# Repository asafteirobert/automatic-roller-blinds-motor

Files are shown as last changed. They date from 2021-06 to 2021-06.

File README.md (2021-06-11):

# Automatic roller blinds motor
Automatic window roller blinds that can be controlled wirelessly using a NRF24L01 module. Controlled either by a small remote, web interface or RESTful API.
Built around an Arduino pro mini and a cheap stepper motor.

For the small remote see this project: [automatic roller blinds small remote](https://github.com/asafteirobert/automatic-roller-blinds-remote).

For the web gateway see this project: [automatic roller blinds web interface](https://github.com/asafteirobert/automatic-roller-blinds-web-ui).

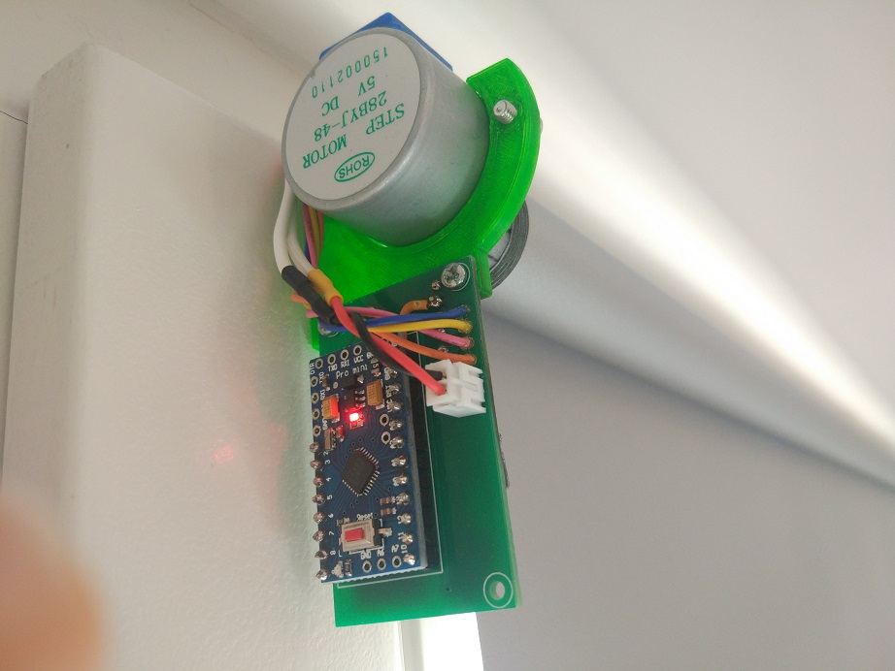
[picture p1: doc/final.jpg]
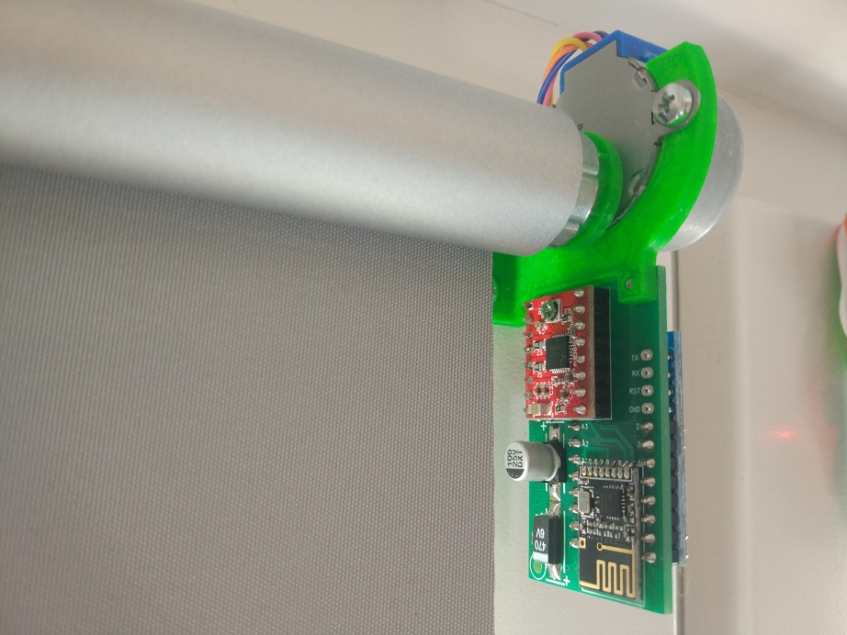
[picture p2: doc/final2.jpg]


https://user-images.githubusercontent.com/6178920/121724726-9242b200-cae8-11eb-8f0c-250091bc018d.mov

## How to use it

This assembly replaces the side of the roller blinds with the string. This means they can no longer be lowered or raised manually.
You will need to route a wire to each window, in order to supply the 9V required.

The blinds are controlled by either the [automatic roller blinds small remote](https://github.com/asafteirobert/automatic-roller-blinds-remote) or the [automatic roller blinds web interface](https://github.com/asafteirobert/automatic-roller-blinds-web-ui), or both.

For more details on how to control and calibrate the blinds, see the related projects linked above. 

## Supported roller blinds

I created this project around a Polish brand(STOL-KAR) of clip-on roller blinds I got from here: https://www.leroymerlin.pl/dekoracja-okien/rolety-i-zaluzje/rolety/roleta-zaciemniajaca-blackout-73-x-150-cm-szara-termoizolacyjna,p575054,l929.html

The shaft has an internal diameter of 18mm.
You will likely need to modify the 3D printed files to adapt for your model. For easier modification, I included the STEP files.

## Limitations and known issues:
- The movement can be slow for some. It takes around 50 seconds to lower and 90 seconds to raise the blinds. Using a bigger stepper motor, such as those used in 3D printers can significantly increase the speed, but would require a much bigger power supply.
- When the blinds are not moving, power is not applied to the stepper motor. This means the blinds can be manually pulled, requiring recalibration.
- There is no encoder, so if the motor gets stuck, misses steps or the blinds are rotated manually, recalibration is needed. Also there are no endstops.

## Making your own
All the required files are included in this project. This includes source code, 3D files to be 3D printed, schematic and PCB.
For instructions see [doc/assembly.md](doc/assembly.md).

## Project status: Finished, active
All intended functionality is implemented and manually tested. I will try to fix major bugs when they are reported. I will review pull requests, but generally I prefer if you fork the project in order to make your own changes and improvements.

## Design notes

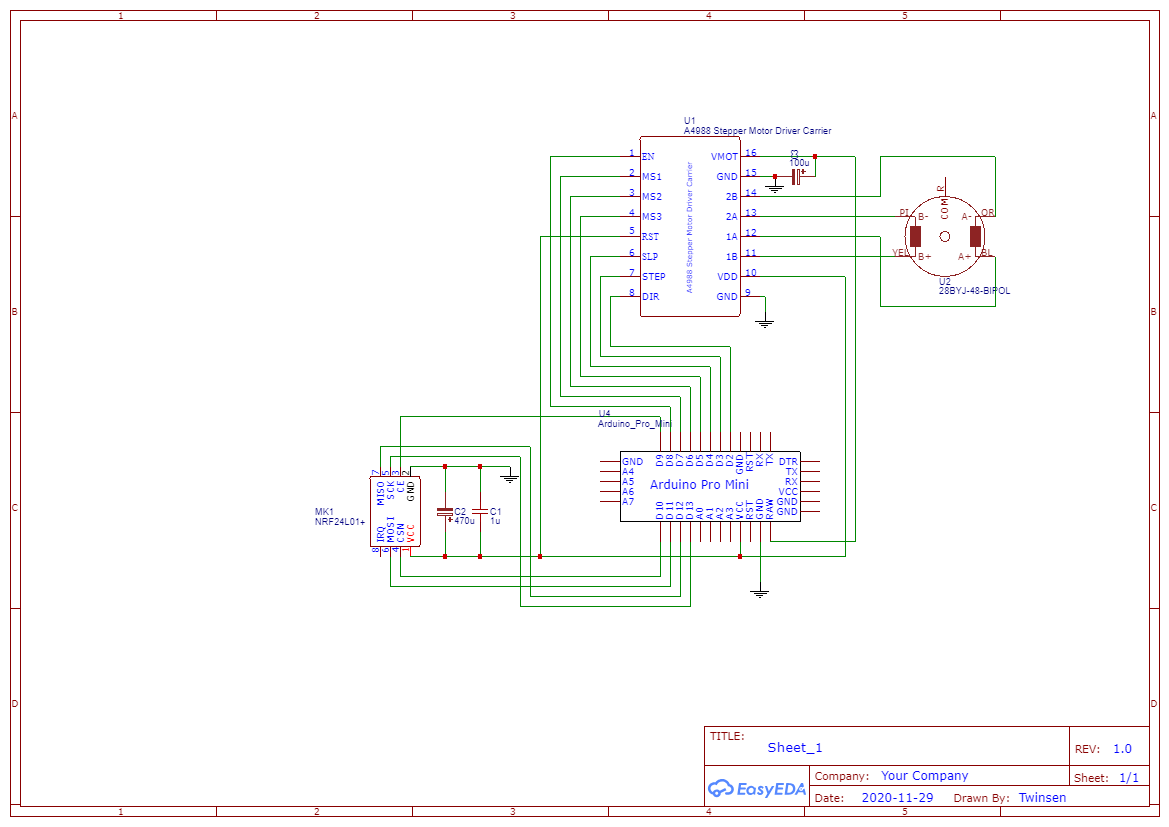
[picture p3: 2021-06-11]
schematic/Schematic_Automatic roller blinds motor_2021-06-11.png

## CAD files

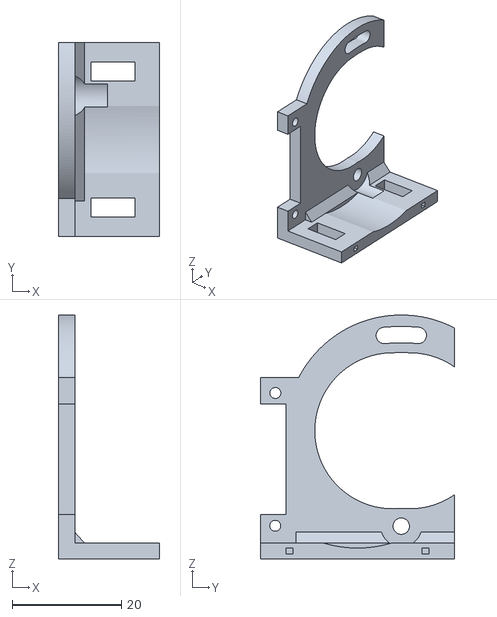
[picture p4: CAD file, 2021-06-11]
3d print/blinds mount.stl
18.5 x 35.5 x 44.6

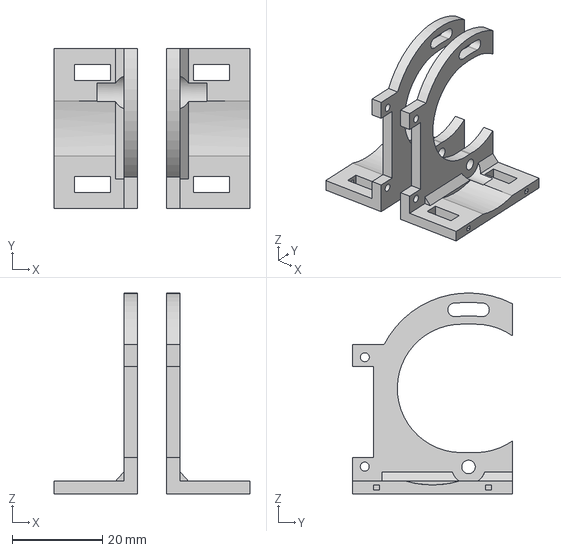
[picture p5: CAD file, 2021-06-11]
3d print/step/blinds mount v12.step
43.5 x 35.5 x 44.6 mm

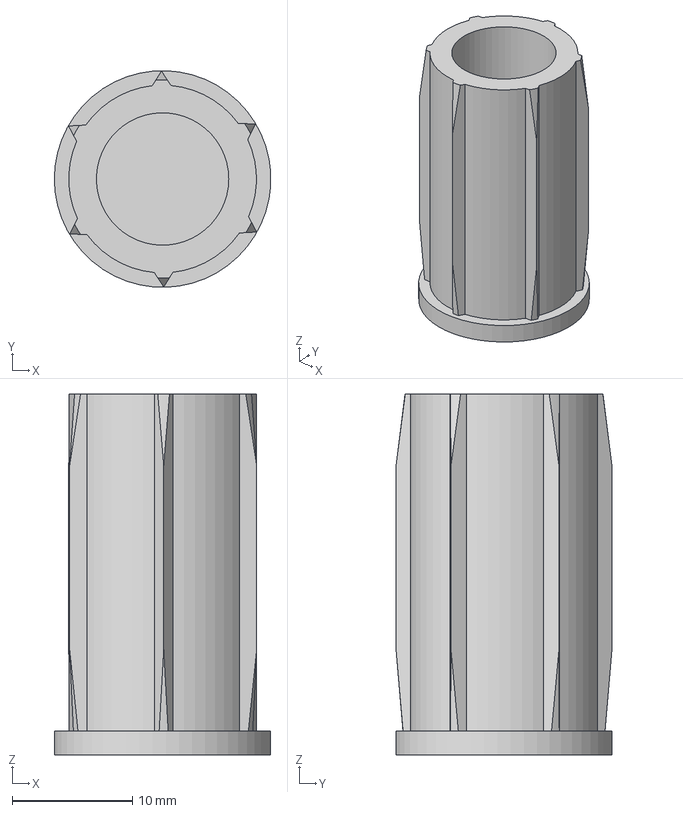
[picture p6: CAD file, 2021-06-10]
3d print/step/blinds motor adapter v11.step
18.0 x 18.0 x 30.0 mm

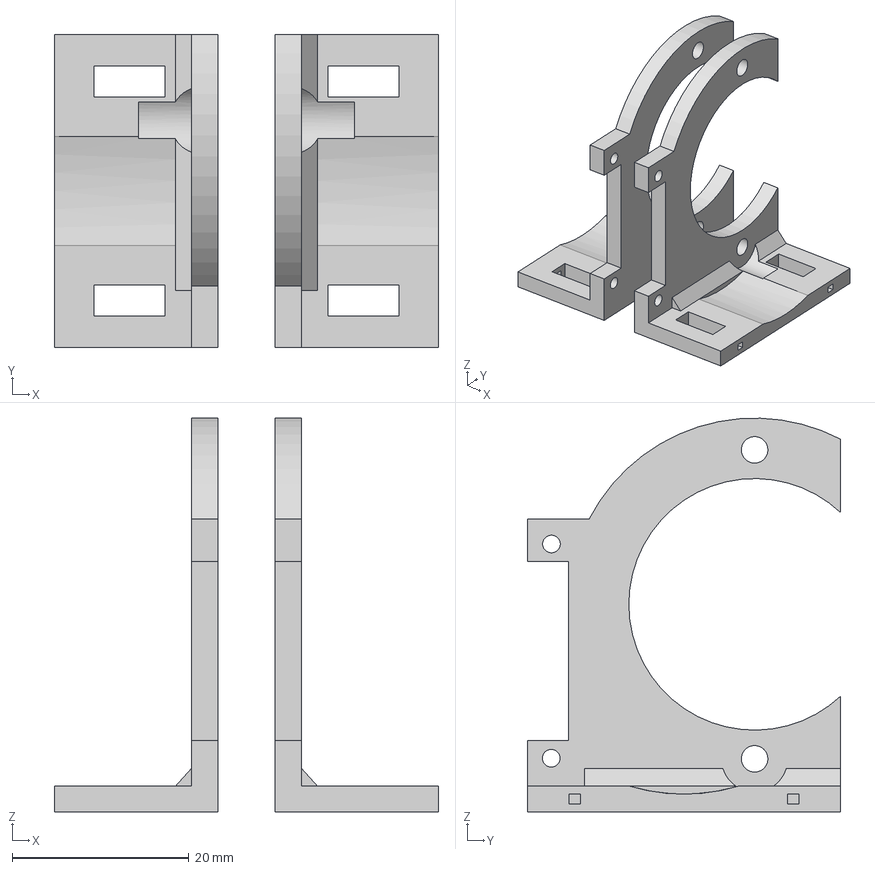
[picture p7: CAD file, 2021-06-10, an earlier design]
3d print/step/blinds mount v11.step
43.5 x 35.5 x 44.6 mm

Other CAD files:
3d print/blinds mount-mirrored.stl
3d print/blinds motor adapter.stl

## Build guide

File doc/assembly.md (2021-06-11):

# Automatic roller blinds motor assembly instructions

For this project you will need a 3D printer, patience, fair soldering skills and some experience with Arduino and Platform IO.

## Materials
- Arduino Pro Mini 3v3
- 28BYJ-48 5V stepper motor
- 0805 1uf SMD capacitor
- 100uF(or higher) 25V SMD type D electrolytic capacitor
- 470uf 6V SMD size C tantalum or type D electrolytic capacitor
- NRF24L01+	SMD module
- A4988 or DRV8825 Stepper Motor Driver module
- 9V power supply (recommended 0.5A multiplied by the number of roller blinds)
- Power supply connector (usually DC2.5/5.5) (optional)
- Wire for connecting power
- Pair of XH 2.54mm 2-pin connectors (optional)
- 3D printed parts found in `3d print` folder. 1x motor adapter and 1x mount(or mount-mirrored)
- PCB
- 2x M2x5 screws
- 2x M3x6 screws
- 2x M3 nuts

## The circuit board
You can find the schematic and PCB in the `schematic` folder. It contains an EasyEDA project and Gerber files.

Or simply order the PCB from this link: https://www.pcbway.com/project/shareproject/Automatic_roller_blinds_motor.html

## Steps

1. Start by converting the 28BYJ-48 stepper motor from unipolar to bipolar. This is done by carefully removing the blue plastic piece and cutting the central trace.
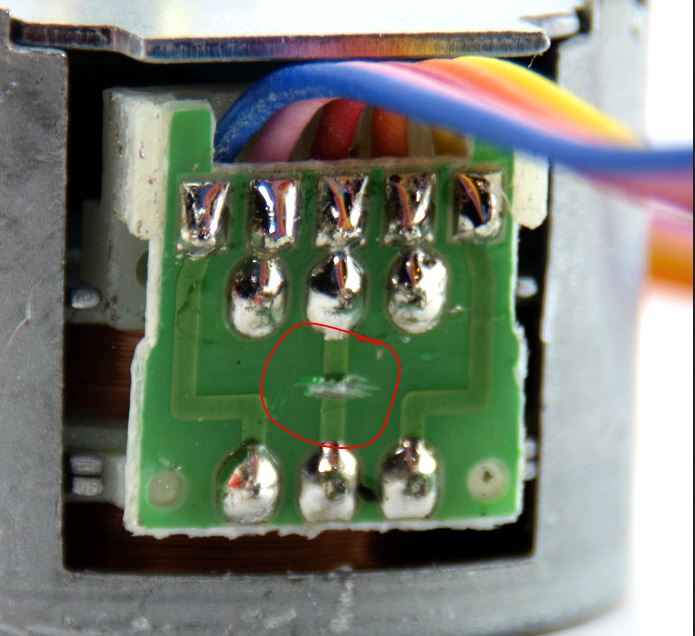
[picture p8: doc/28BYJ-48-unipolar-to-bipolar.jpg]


2. Solder the pin headers for the Arduino Pro Mini and cut the excess pin length. Pin headers only, otherwise you can't do the next step.
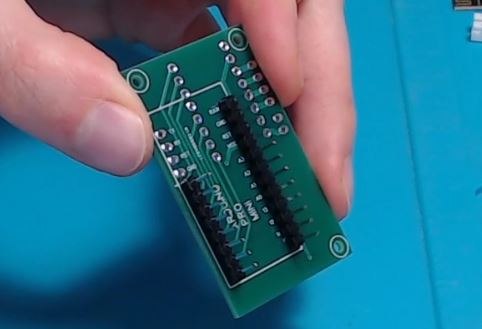
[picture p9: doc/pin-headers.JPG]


3. Solder the A4988 or DRV8825 stepper motor driver module and cut the excess pin length.
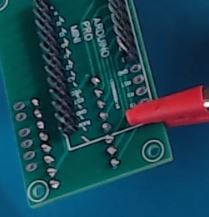
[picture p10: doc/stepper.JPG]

4. Solder the Arduino Pro Mini to the pin header and cut the excess pin length.
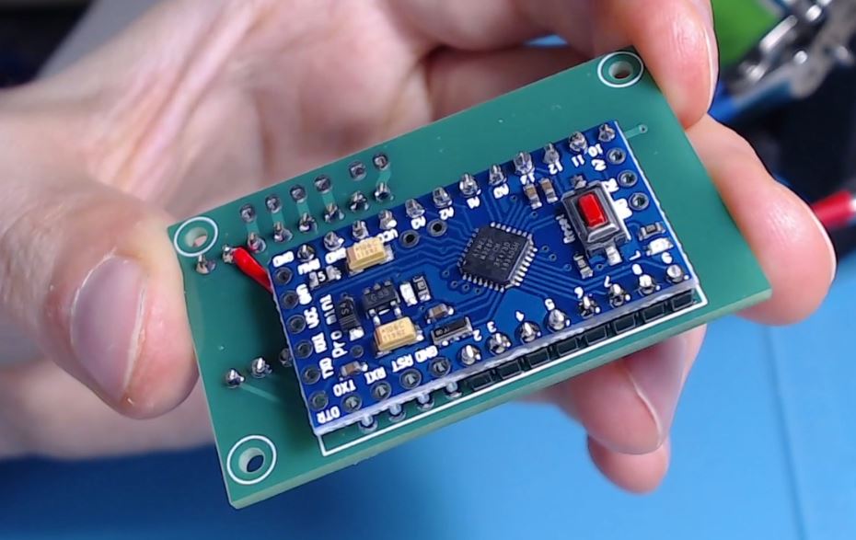
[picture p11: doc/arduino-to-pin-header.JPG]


5. Solder the rest of the components to the PCB. Use double sided tape for the NRF24L01 module to make sure it doesn't touch the nearby pins.
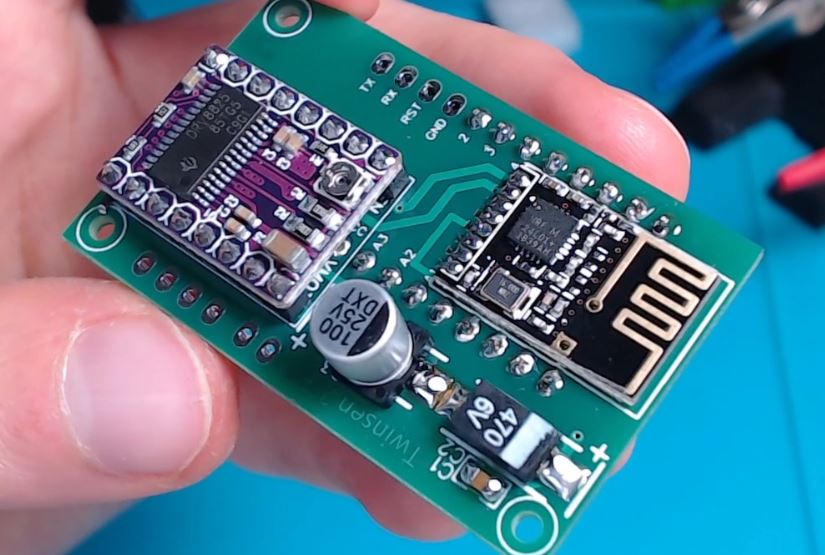
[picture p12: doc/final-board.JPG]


6. Secure the stepper motor to the 3D printed part using M3x6 screws and M3 nuts
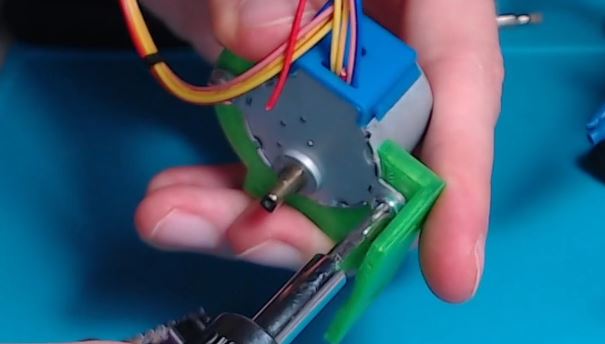
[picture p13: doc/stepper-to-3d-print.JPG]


7. Secure the PCB to the 3D printed part using M2x5 screws. You can choose the orientation and side that is best for you.
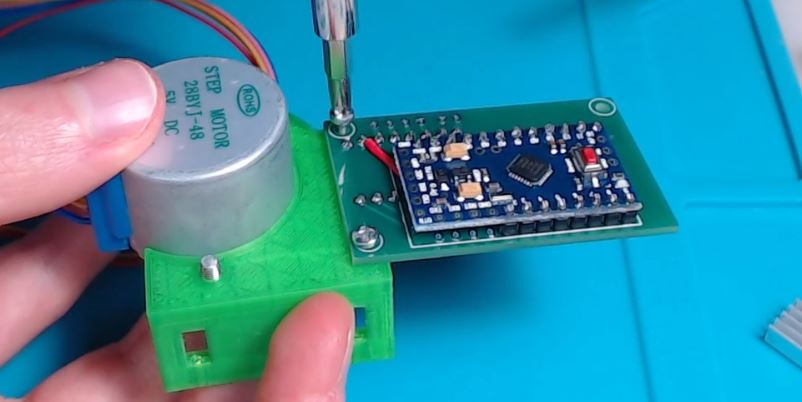
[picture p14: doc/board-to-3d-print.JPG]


8. Solder the stepper motor to the PCB as follows: 2B - Orange, 2A - Pink, 1A - Blue, 1B - Yellow. If the motor is facing right, reverse the Blue and Yellow wires; alternatively, you can change the motor direction by changing `STEPPER_REVERSE` in `Constants.h`
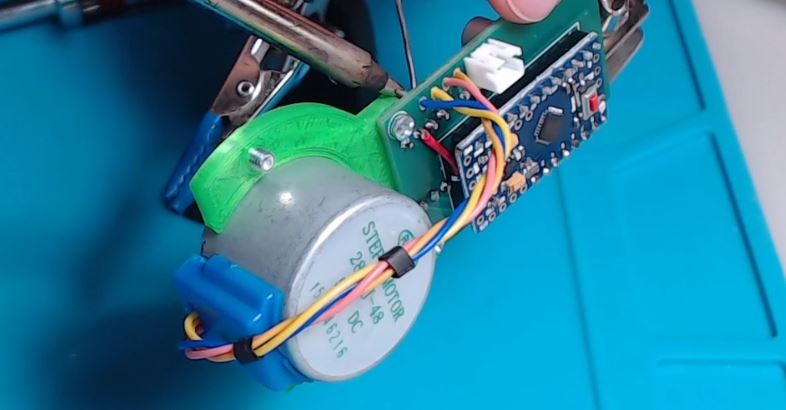
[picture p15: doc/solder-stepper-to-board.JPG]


9. Open this project in Platform IO.
10. Open `Constants.h` and change `ROOM_NUMBER` and `BLIND_NUMBER`. This pair needs to be unique for every window blind. One remote can only control the blinds in one room. The values can't be 0.
11. Compile and upload the project. You will need a USB serial adapter.
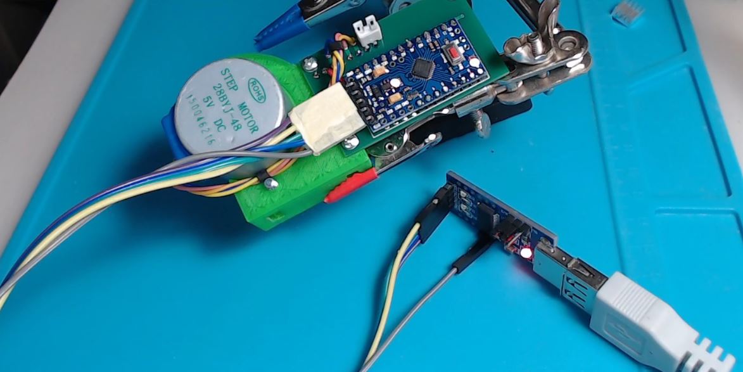
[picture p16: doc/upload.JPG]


12. Check everything and perform first test. You will need either the remote or the web interface
13. Connect the actual roller blinds using the 3D printed motor adapter. Carefully mount it to your window using the original clips or using screws.
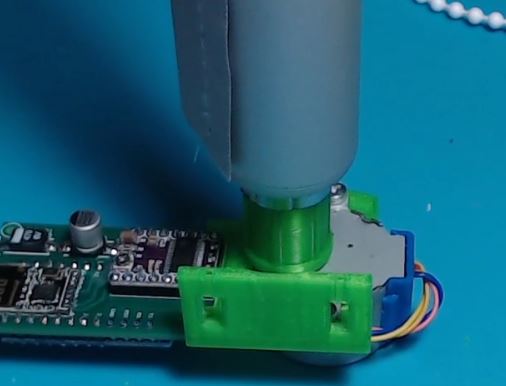
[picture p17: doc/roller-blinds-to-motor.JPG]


14. Adjust the height of the motor using the screw on the side, so the blinds are perfectly horizontal.
15. Route the wire from the power supply and solder or connect it using XH 2.54mm connectors.


Note: some pictures are slightly different, as I made adjustments and improvements to the PCB and 3D printed parts.

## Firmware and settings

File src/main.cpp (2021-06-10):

#include <Arduino.h>
#include "Constants.h"
#include "SavedData.h"
#include <SPI.h>
#include <RF24.h>
#include <AccelStepper.h>

//#define DEBUG

#ifdef DEBUG
#define DEBUG_PRINT(x)  Serial.println (x)
#include "printf.h"
#else
#define DEBUG_PRINT(x)
#endif

struct ReturnDataType
{
  uint8_t roomId;
  uint8_t blindId;
  int8_t currentTargetPercent;
};

//Special values written in targetPercent for various commands
static constexpr int8_t TARGET_DISCOVER = -1; //does nothing, just send the latest ack packet
static constexpr int8_t TARGET_SET_START = -2;
static constexpr int8_t TARGET_SET_END = -3;
static constexpr int8_t TARGET_MOVE_BACK = -4;
static constexpr int8_t TARGET_MOVE_FWD = -5;

struct SentDataType
{
  int8_t targetPercent;
  uint8_t speed;
};

SentDataType sentData;
ReturnDataType returnedData;

// RF24 object for NRF24 communication
RF24 radio(PIN_NRF_CE, PIN_NRF_CS);

AccelStepper motor(AccelStepper::DRIVER, PIN_MOTOR_STEP, PIN_MOTOR_DIR);

unsigned long lastRadioCheck = 0;
unsigned long lastCalibrationCommand = 0;

SavedData savedData;

void setup()
{
#ifdef DEBUG
  Serial.begin(9600);
#endif
  DEBUG_PRINT(F("Starting..."));

  //Load what we think was the last state
  //Note that state is only saved in some cases to avoid trashing the EEPROM
  savedData.loadFromEEPROM();

	pinMode(PIN_MOTOR_STEP, OUTPUT);
	pinMode(PIN_MOTOR_DIR, OUTPUT);
	pinMode(PIN_MOTOR_SLP, OUTPUT);
	pinMode(PIN_MOTOR_MS3, OUTPUT);
	pinMode(PIN_MOTOR_MS2, OUTPUT);
	pinMode(PIN_MOTOR_MS1, OUTPUT);
	pinMode(PIN_MOTOR_EN, OUTPUT);

  digitalWrite(PIN_MOTOR_MS1, HIGH);
  digitalWrite(PIN_MOTOR_MS2, LOW);
  digitalWrite(PIN_MOTOR_MS3, LOW);

  digitalWrite(PIN_MOTOR_EN, LOW);
  digitalWrite(PIN_MOTOR_SLP, HIGH);

  motor.setMaxSpeed(STEPPER_MAX_SPEED);
	motor.setAcceleration(STEPPER_ACCELERATION);
  motor.setPinsInverted(STEPPER_REVERSE);

  returnedData.roomId = ROOM_NUMBER;
  returnedData.blindId = BLIND_NUMBER;
  returnedData.currentTargetPercent = savedData.currentTargetPercent;

  motor.setCurrentPosition((savedData.totalLengthSteps*savedData.currentTargetPercent)/100);

  // Start radio communication
  radio.begin();
  radio.setChannel(NRF_CHANNEL);
  radio.setPALevel(RF24_PA_MAX);
  radio.setDataRate(RF24_250KBPS);
  radio.enableAckPayload();
  radio.enableDynamicPayloads();
  radio.openReadingPipe(1, NRF_PIPE);
  radio.startListening();
  //Ack payloads are handled automatically by the radio chip when a payload is received.
  //Users should generally write an ack payload as soon as startListening() is called, so one is available when a regular payload is received.  
  radio.writeAckPayload(1, &returnedData, sizeof(returnedData));

#ifdef DEBUG
  printf_begin();
  radio.printDetails();
#endif
}

void loop()
{
  unsigned long currentMillis = millis();
  bool motorIsRunning = true;
	if (!motor.run())
  {
		motor.disableOutputs();
    digitalWrite(PIN_MOTOR_SLP, LOW);
    motorIsRunning = false;
  }

  //don't check the radio very often when the motor is running
  //check constantly when doing calibration
  if ((!motorIsRunning && (currentMillis - lastRadioCheck > 100)) ||
      (currentMillis - lastRadioCheck > 1000) ||
      (currentMillis - lastCalibrationCommand < 1000))
  {
    lastRadioCheck = currentMillis;
    // If transmission is available
    uint8_t pipeNum;
    if (radio.available(&pipeNum))
    {
      uint8_t len = radio.getDynamicPayloadSize();
      if (pipeNum == 1 && len == sizeof(sentData))
      {
        radio.read(&sentData, sizeof(sentData));
        if (sentData.targetPercent >= 0)
        {
          savedData.currentTargetPercent = sentData.targetPercent;
          digitalWrite(PIN_MOTOR_SLP, HIGH);
          motor.enableOutputs();
          long newPosition = (savedData.totalLengthSteps*sentData.targetPercent)/100;
          motor.setMaxSpeed(STEPPER_MAX_SPEED*sentData.speed/100*(motor.currentPosition() < newPosition?STEPPER_MOVE_DOWN_MULTIPLIER:1));
          motor.moveTo(newPosition);
          savedData.saveToEEPROM();
        }
        else if (sentData.targetPercent == TARGET_MOVE_BACK)
        {
          digitalWrite(PIN_MOTOR_SLP, HIGH);
          motor.enableOutputs();
          motor.setMaxSpeed(STEPPER_MAX_SPEED*sentData.speed/100);
          //TARGET_MOVE_* is sent every 100ms, so move enough for 100ms plus the distance it takes to decelerate
          long stepsToTake = (long)((motor.maxSpeed() * motor.maxSpeed()) / (2.0 * STEPPER_ACCELERATION)) + 1 + motor.maxSpeed()/10;
          motor.move(-stepsToTake);
          savedData.currentTargetPercent = (motor.targetPosition()*100)/savedData.totalLengthSteps;
          lastCalibrationCommand = currentMillis;
        }
        else if (sentData.targetPercent == TARGET_MOVE_FWD)
        {
          digitalWrite(PIN_MOTOR_SLP, HIGH);
          motor.enableOutputs();
          motor.setMaxSpeed(STEPPER_MAX_SPEED*sentData.speed/100);
          //TARGET_MOVE_* is sent every 100ms, so move enough for 100ms plus the distance it takes to decelerate
          long stepsToTake = (long)((motor.maxSpeed() * motor.maxSpeed()) / (2.0 * STEPPER_ACCELERATION)) + 1 + motor.maxSpeed()/10;
          motor.move(stepsToTake);
          savedData.currentTargetPercent = (motor.targetPosition()*100)/savedData.totalLengthSteps;
          lastCalibrationCommand = currentMillis;
        }
        else if (sentData.targetPercent == TARGET_SET_START)
        {
          digitalWrite(PIN_MOTOR_SLP, HIGH);
          motor.enableOutputs();
          motor.moveTo(motor.currentPosition()); //in case we are moving, decelerate, stop and move back
          motor.runToPosition(); //block until we are stopped
          savedData.totalLengthSteps -= motor.currentPosition(); //keep the end position
          motor.setCurrentPosition(0);
          savedData.currentTargetPercent = 0;
          savedData.saveToEEPROM();
          lastCalibrationCommand = currentMillis;
        }
        else if (sentData.targetPercent == TARGET_SET_END)
        {
          digitalWrite(PIN_MOTOR_SLP, HIGH);
          motor.enableOutputs();
          savedData.totalLengthSteps = motor.currentPosition();
          motor.moveTo(motor.currentPosition()); //in case we are moving, decelerate, stop and move back
          //no need to block, motor will continue it's movement in main loop
          savedData.currentTargetPercent = 100;
          savedData.saveToEEPROM();
          lastCalibrationCommand = currentMillis;
        }
        returnedData.currentTargetPercent = savedData.currentTargetPercent;
        DEBUG_PRINT("Received " + String(sentData.targetPercent));
      }
      else
      {
        radio.flush_rx();
        delay(2);
        DEBUG_PRINT("Discarded bad packet <<<");
      }
      //always set ack payload for next packet, even if we got bad packet now
      radio.flush_tx(); //make sure we always have one ack payload
      radio.writeAckPayload(1, &returnedData, sizeof(returnedData));
    }
  }
}

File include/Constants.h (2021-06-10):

#ifndef _CONSTANTS_h
#define _CONSTANTS_h
#include "arduino.h"

// ======= Configuration =======
const static uint8_t ROOM_NUMBER = 2;
const static uint8_t BLIND_NUMBER = 2; //window number

const static float STEPPER_MAX_SPEED = 1000; //steps per second
const static float STEPPER_ACCELERATION = 1000; //steps per second per second
const static bool STEPPER_REVERSE = true;

const static float STEPPER_MOVE_DOWN_MULTIPLIER = 1.8; //when moving down, move at higher speed

// ======= NRF =======
const static uint8_t NRF_PIPE[5] = {BLIND_NUMBER, ROOM_NUMBER, 0x0e, 0xf1, 0xbf};
const static uint8_t NRF_CHANNEL = 103;

// ======= Pin defination =======
const uint8_t PIN_NRF_CE = 9;
const uint8_t PIN_NRF_CS = 10;
const uint8_t PIN_MOTOR_DIR = 2;
const uint8_t PIN_MOTOR_STEP = 3;
const uint8_t PIN_MOTOR_SLP = 4;
const uint8_t PIN_MOTOR_MS3 = 5;
const uint8_t PIN_MOTOR_MS2 = 6;
const uint8_t PIN_MOTOR_MS1 = 7;
const uint8_t PIN_MOTOR_EN = 8;

#endif

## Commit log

2021-06-10 Initial project
    [blinds motor adapter v11.step, blinds motor adapter.stl, blinds mount v11.step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]
2021-06-10 Fixed image in assembly.md
2021-06-11 Added room for height adjustment in the mounting part
    [blinds mount v12.step, blinds mount-mirrored.stl, blinds mount.stl]
2021-06-11 Added PCB order link
2021-06-11 Added schematic image
2021-06-11 Moved STEP file to correct folder
    [blinds mount v12.step]
